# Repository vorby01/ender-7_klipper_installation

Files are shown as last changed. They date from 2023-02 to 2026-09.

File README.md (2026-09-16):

# Ender-7 Klipper Install
Details for Installing Klipper on Creality Ender 7 with BLTouch (Use at own risk)(Work in Progress)
- The ender-7 was my first 3d printer and these files show my learning curve into FDM printing with the ender-7

- Notes:
  - Ender-7 inbuilt screen will no longer work, incompatable with Klipper (creality wont release source code)
  - Installing Klipper if settings are incorrect the printer can crash/break
  
- - - -
- ### Printer Details
  - #### Creality Ender-7 Core-XY 3D Printer
    - (Early model with leadshine DM542 microstep drivers for X and Y)(purchased 2021/08/08)
  - ##### Modifications (2023/01/21) (as of)
    - Creality BL Touch Auto Bed Leveling Kit for Ender-7 (No Longer Available)(https://www.creality3d.online/collections/auto-bed-leveling-kit)
    - Embrace Making, Creality Ender 7 PEI Magnetic Flex Build Plate (https://embracemaking.com/products/copy-of-pei-magnetic-flex-build-plate-systems)
    - Tiny Machines 3D, Ender 7 Bed Stability Upgrade + Z-Axis Linear Rail Upgrade (https://www.tinymachines3d.com/products/ender-7-z-axis-upgrade-with-linear-rails-and-dual-lead-screws)
    - TH3D, Aluminum Bed Spacers (https://www.th3dstudio.com/product/aluminum-bed-spacers-pack-of-4/)

  - ##### Modifications (2023/02/18)
    - ADXL345 (Klipper Resonance Compensation)

  - ##### Modifications (2023/07/16)
    - Mosquito Magnum Hotend (New 50w Heater, Thermister(300))
    - Lgx Lite Extruder (Direct Drive)
    - Custom designed mounts for hotend and extruder on printables.com

- - - -           
- ### Klipper Host Machine
  - Raspberry Pi4
    - Running: Mainsail OS

- - - -
20260917 updated to markdown syntax
## File Descriptions:
- 00_Prerequisite info.md - Some information the should be collected before starting, eg, default firmware settings(Marlin: M503), microcontroller/board(Creality CR-FDM-v2.4.S1_v101), pin hardware names

- 01_Install mainsailOS.md - Process to install MainsailOS on raspberry pi

- 02_Klipper config and install.md - Process to build klipper printer.cfg and flash microcontroller/board

- 03_Testing and calibration.md - Process for testing klipper is functional and ready to print

- 04_Klipper macros.md - Some Klipper macros and using with PrusaSlicer

- 05_Extruder maximum flow.md - Processes for determing printers maximum flow rate/speed

- 06_Pressure advance.md - Configure and use klipper pressure advance

- 07_Resonance compensation.md - Install and use ADXL345 accelerometer to minimise printer resonance (input shaping) (max_accel: x_max=18400, y_max=11500)
 
## Pictures
### Ender 7 2023/01/21
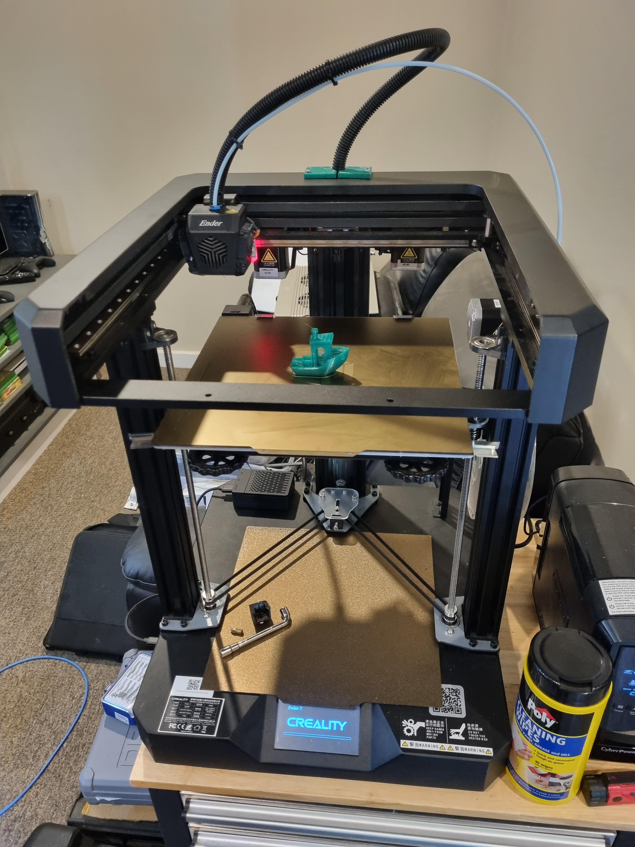
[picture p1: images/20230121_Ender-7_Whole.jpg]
Ender-7


### Ender 7 2023/07/16
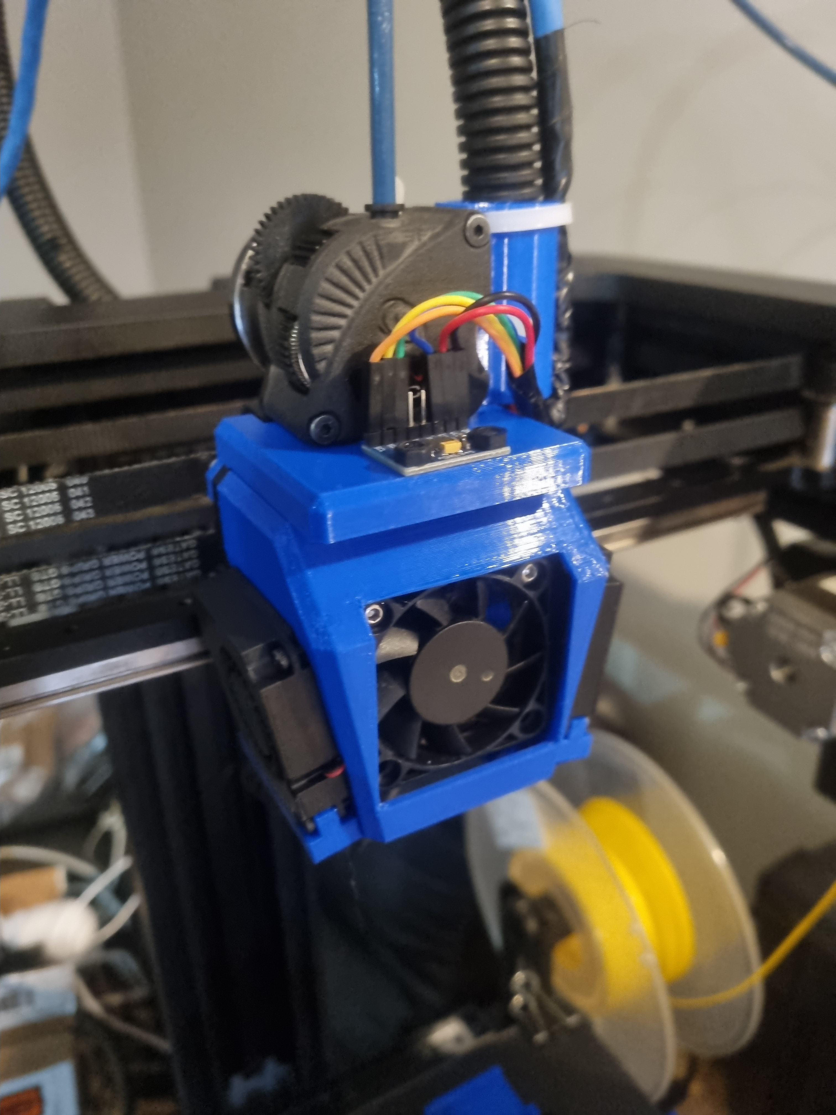
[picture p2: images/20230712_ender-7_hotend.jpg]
Ender-7_mosquito_magnum


### Ender-7 2023/08/17 hotend_upgrade_v2
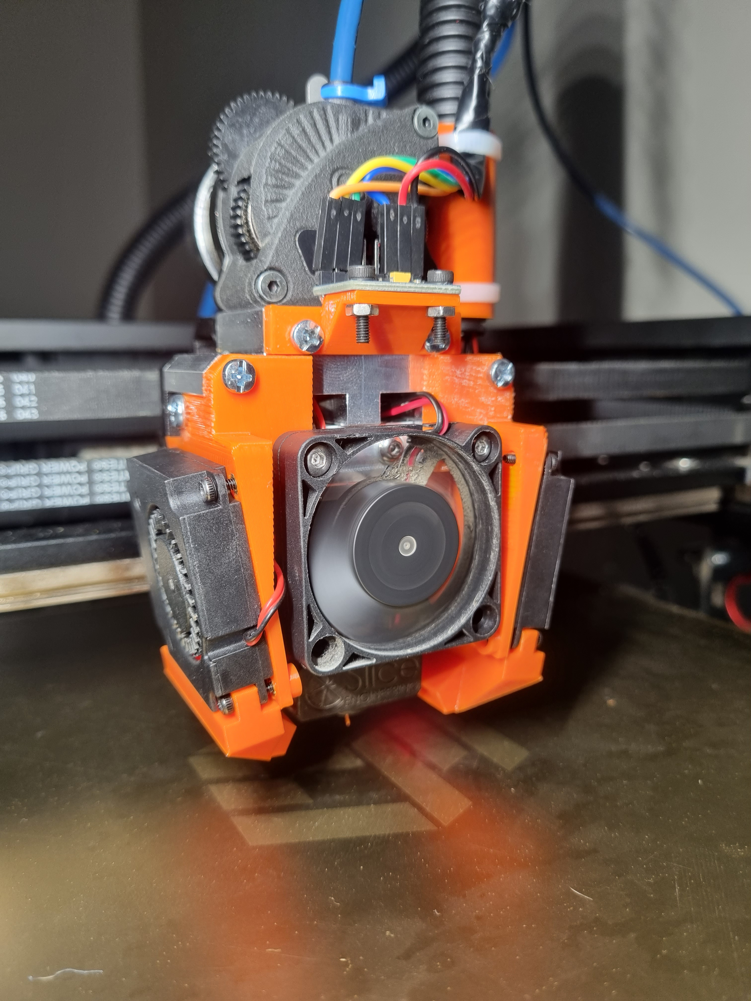
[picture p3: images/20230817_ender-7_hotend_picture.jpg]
Ender-7_mosquitto_magnum_v2


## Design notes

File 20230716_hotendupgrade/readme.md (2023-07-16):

Creality Ender-7 Hotend Upgrade to Mosquito Magnum and Lgx Lite extruder as direct drive

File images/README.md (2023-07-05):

###### Max Extrusion Test 80mm/s to 250mm/s
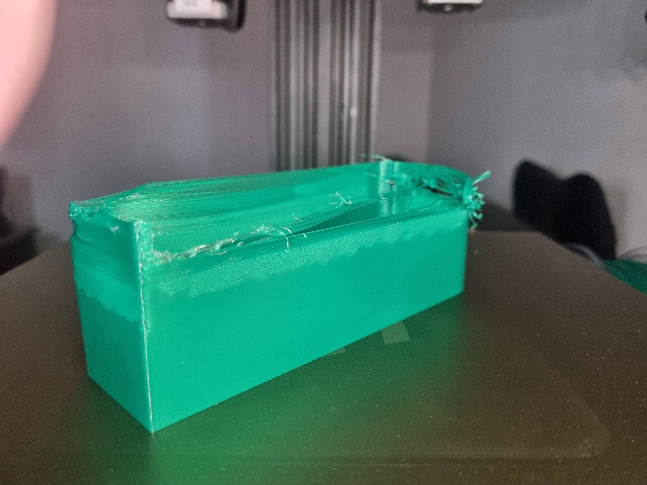
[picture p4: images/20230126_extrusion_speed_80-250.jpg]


##### Ender-7 ADXL345 Mount
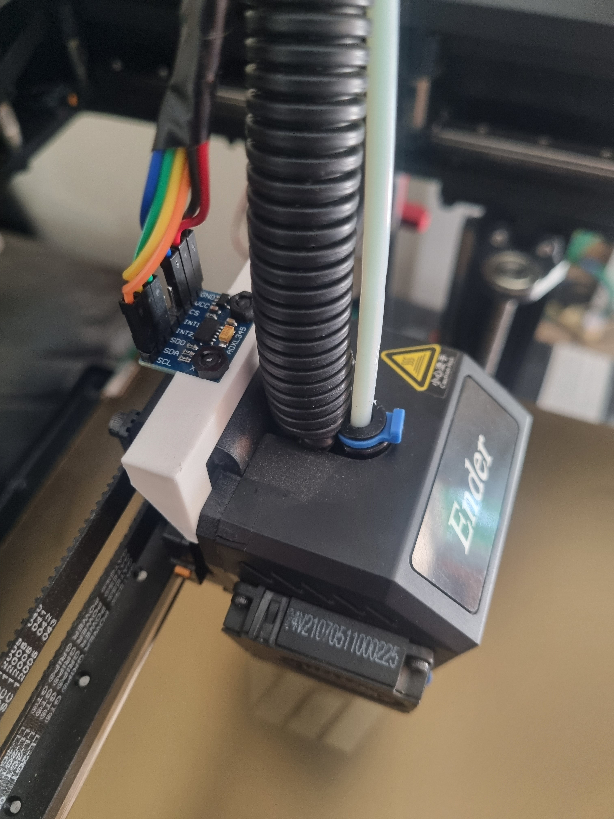
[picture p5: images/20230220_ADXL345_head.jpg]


###### Kilpper First Benchy 21/01/23 (2h 22m) (PrusaSlicer Base Ender 7 settings) 
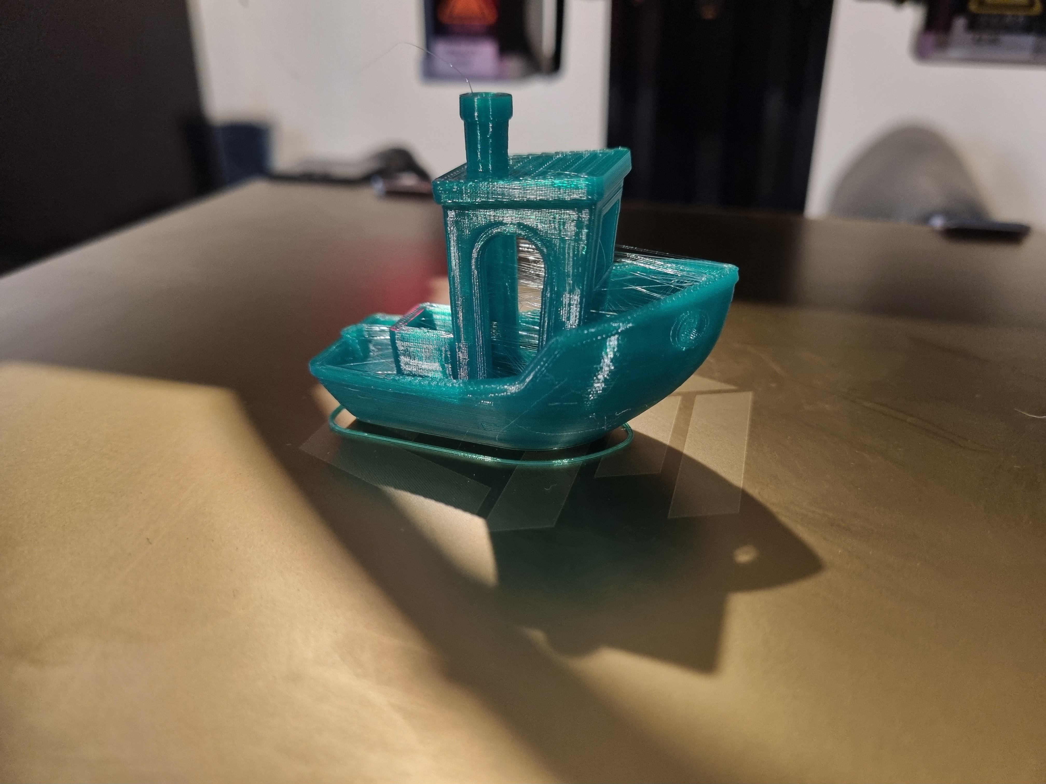
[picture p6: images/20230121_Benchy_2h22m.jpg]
benchy1


###### Benchy 23/01/23 (1h 32m)
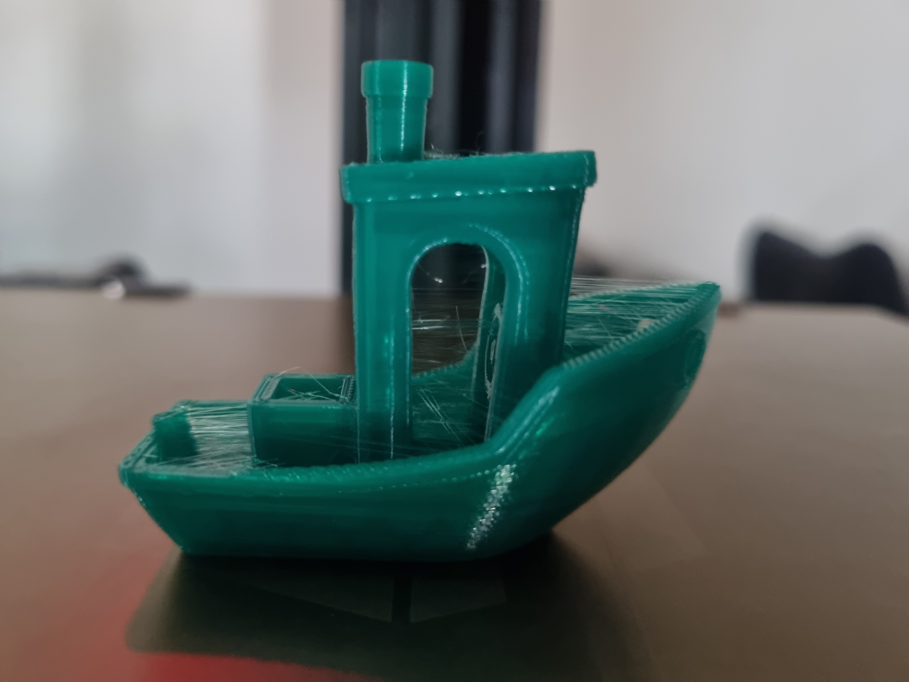
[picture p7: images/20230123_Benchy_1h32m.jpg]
benchy2


###### Benchy 24/01/23 (1h 20m)
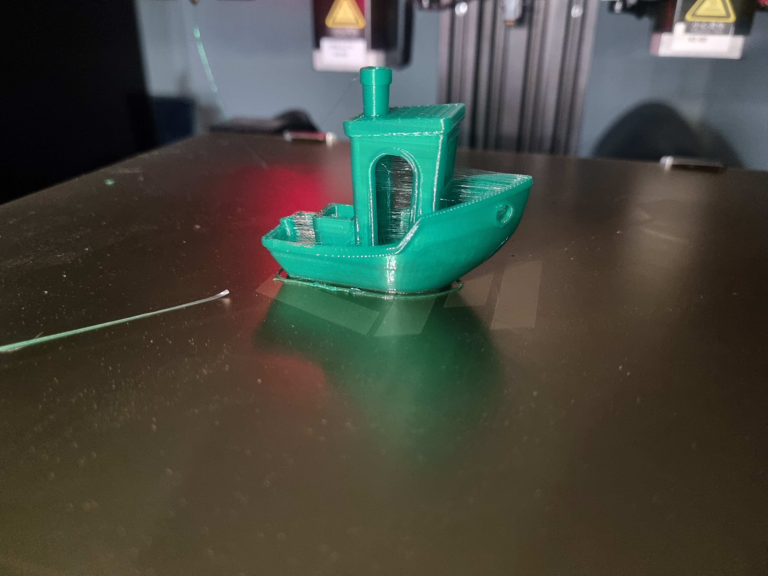
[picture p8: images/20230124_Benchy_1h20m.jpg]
benchy3


###### Benchy 05/07/23 (40m)
20230705 3DBenchy 40min (Top/Bottom Layers,3)(Perminiters,2)(Infill,10%)
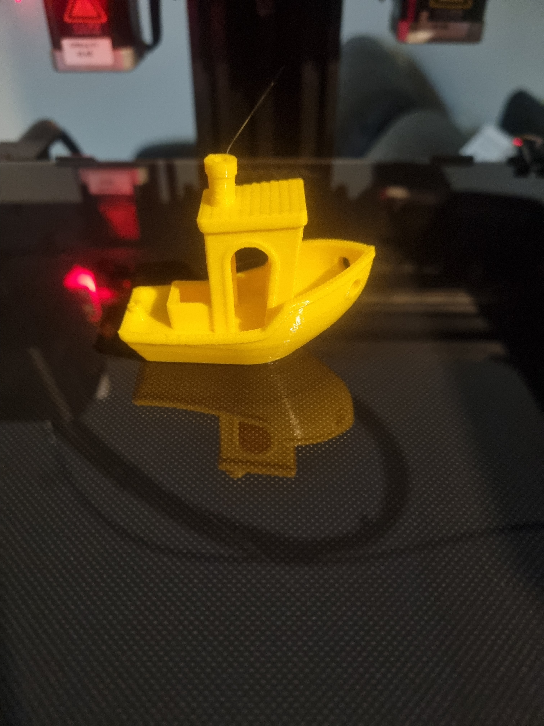
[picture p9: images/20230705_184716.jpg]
Ender-7


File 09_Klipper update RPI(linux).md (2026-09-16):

## 09_Klipper update RPI(linux)

#### Update Klipper on rpi(raspberry pi) to match updated mcu version
  - 20250125

  - SSH to RPi  
    `ssh pi@<ip_address>`

  - Navigate to Klipper directory  
    `cd ~/klipper/`

  - Klipper configure firmware
    `make menuconfig`

  - change micro-controller architecture to linux process
  - remove !PA15 (possibly still showing from mcu firmware update)

**make menuconfig (CUI)**
```
[*] Enable extra low-level configuration options
    Micro-controller Architecture (Linux proces) --->
() GPIO pins to set at micro-controller startup
```

  - Compile Klipper firmware for rpi
    - Stop Klipper service  
      `sudo service klipper stop`

    - Compile firmware  
      `make flash`

    - Start Klipper service  
      `sudo service klipper start`

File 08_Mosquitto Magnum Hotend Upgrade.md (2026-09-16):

## 08_Mosquitto Magnum Hotend Upgrade

- #### Hotend Blower Fans (EFC-04D24L) 
  - Yellow = positive, Blue = negative
  - replaced stock fans due to fault on one.

- #### Lgx Lite Extruder
  - Connector: JST-XH 4-pin connector
  - Motor gear : 10 teeth
  - Motor length: 20 mm
  - Motor Diameter: 36mm
  - Step Angle : 1.8 degree (200 steps per rotation)
  - Max Torque at : 1800 PPS
  - Max operating Temperature / Current : 120℃ / 750 mA
  - Manufacturer : LDO
  - Manufacturer SKU : LDO-36STH20-1004AHG(XH)
  - retraction speed : 35 mm/s
  - retraction distance (bowden) : ~5 mm (0.4 + tube length[mm] x 0.015)
  - retraction distance (direct drive) for rigid materials : 0.4 mm
  - retraction distance (direct drive) for soft materials : 3 mm

- #### Change of stepper motor will require adjustment of Vref for extruder (Default reading Vref 1.19v)
  - Formula for TMC stepper drivers is Vref = `( I * 2.5 ) / Imax`
    - I is the target current value measured in Amps 
    - Imax is 1.77 on regular mode and 1.2 on SilentStepSticks mode
  - Bondtech recommended vref of between .45 - .65

- min vref (0.45 * 2.5) / 1.77 = 0.64
- max vref (0.65 * 2.5) / 1.77 = 0.92
> vref between 0.67v - 0.92v

(0.55 * 2.5) / 1.77 = 0.78v

- #### Update Klipper Config to suit Lgx Lite Extruder
  - e-steps value : 562 using 16 microsteps; 1124 using 32 microsteps. 
  - rotation_distance = `full_steps_per_rotation * microsteps / steps_per_mm`
  - rotation_distance = 200 * 16 / 562
  > rotation_distance = 5.7

  - Change extruder direction to suit Lgx-Lite Extruder

**printer.cfg**
```
[extruder] #Driver, Creality Board (TMC2208) (Lgx-Lite Extruder)
dir_pin: PB3  #!PB3 = default direction, PB3 = reverse extruder dimension
```

- #### Update Klipper Config to suit new thermister
  - Slice engineering thermister(300)(ATC Semitec 104NT-4-R025H42G)

**printer.cfg**
```
[extruder] #Driver, Creality Board (TMC2208) (Lgx-Lite Extruder)
sensor_type: ATC Semitec 104NT-4-R025H42G
```

  - Calibrate new thermister  
    `PID_CALIBRATE HEATER=extruder TARGET=215`

  - Calibrate new nozzle offset  
    `PROBE_CALIBRATE`

- #### 2023_07_19 Input shaping (Resonance Compensation)
  - Check connection to accelerometer in mainsailos  
    `ACCELEROMETER_QUERY`
    
  - Measure axes noise (range ~1-100) (1000+ quality issues)  
    `MEASURE_AXES_NOISE`

  - Measure resonance (per axis)(generates CSV files)  
    `TEST_RESONANCES AXIS=X`  
    `TEST_RESONANCES AXIS=Y`

  - Process generated CSV files (Requires SSH login)  
    `~/klipper/scripts/calibrate_shaper.py /tmp/resonances_x_*.csv -o /tmp/shaper_calibrate_x.png`
    > output:  
    Fitted shaper 'mzv' frequency = 63.2 Hz (vibrations = 0.0%, smoothing ~= 0.051)  
    To avoid too much smoothing with 'mzv', suggested max_accel <= 11800 mm/sec^2

    `~/klipper/scripts/calibrate_shaper.py /tmp/resonances_y_*.csv -o /tmp/shaper_calibrate_y.png`
    > output:  
    Fitted shaper 'mzv' frequency = 45.2 Hz (vibrations = 1.3%, smoothing ~= 0.100)  
    To avoid too much smoothing with 'mzv', suggested max_accel <= 6000 mm/sec^2

  - Update klipper printer.cfg

**printer.cfg**
```
[input_shaper]
shaper_type_x: mzv
shaper_freq_x: 63.2
shaper_type_y: mzv
shaper_freq_y: 45.2

[printer]
max_accel: 10000           #x_max=11800, y_max=6000
```

  - To recalibrate after adjustment (Input Shaper auto-calibration (re-calibration)(does not update max_accel))  
    `SHAPER_CALIBRATE`  
    `SAVE_CONFIG`

- #### 2023_08_15 Pressure Advance Tuning
  - 0.4mm nozzle brass

  - Slicer 
    - Set zero infill, and a coarse layer height (the layer height should be around 75% of the nozzle diameter). Make sure any "dynamic acceleration control" is disabled in the slicer.
    - Layer Height: 0.75 * 0.4 = 0.3
    - Layer Width: 1.1 * 0.4 = 0.44
    - Estimated volume: 0.44mm * 0.3mm * 100mm/s = 13.2mm^3/sec

  - Klipper  
    `SET_VELOCITY_LIMIT SQUARE_CORNER_VELOCITY=1 ACCEL=500`  
    `TUNING_TOWER COMMAND=SET_PRESSURE_ADVANCE PARAMETER=ADVANCE START=0 FACTOR=.005`

  - Start tuning tower print

  - Measure print
  - Calculate pressure advance value
    - pressure_advance = `<start> + <measured_height> * <factor>`
    0 + 30 * 0.005 = 0.15
    > pressure_advance = 0.15

  - Update klipper printer.cfg

**printer.cfg**
```
[extruder]
pressure_advance = 0.15
```

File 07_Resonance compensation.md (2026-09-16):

## 07_Resonance compensation

### Resonance compensation (requires ADXL345)
- Mount ADXL345 to print head securely
  - print mounting bracket: 20230216_ADXL345_Mount.3mf (printed on prusa_mini+)

- ##### ADXL345 to RaspberryPi4 wiring

| CAT5 cable colours |  |
|---|---|
| Green  | Green-White  |
| Orange | Orange-White |
| Blue | Blue-White |
| Brown  | Brown-White  |

- Recommended twisted pairing (minimum interferance) (SPI wiring)
  - GND+MISO
  - 3.3V+MOSI
  - SCLK+CS

- Raspberry Pi Wiring

| RPi pinout |  | | | | |
|-----|---|---|---|---|---|
| Pin | GPIO | ADXL345 | SPI  | Colour | CAT5 |
| 17  | 3.3v | VCC | VCC  | RED | Orange |
| 19  | GPIO 10 | SDA | MOSI | YELLOW | Orange-White |
| 20  | GND | GND | | BLACK  | Green-White  |
| 21  | GPIO 9  | SDO | MISO | GREEN  | Green |
| 23  | GPIO 11 | SCL | SCLK | ORANGE | Blue-White |
| 24  | GPIO 8  | CS | CS | BLUE | Blue |

- RPi4 to ADXL345 wiring (CAT5 pairs)

| ADXL345 pinout | | |
|---|---|---|
| ADXL345 | Colour | CAT5 Colour  |
| | | |
| GND | BLACK  | Green-White  |
| SDO | GREEN  | Green |
| | | |
| 3.3 | RED | Orange |
| SDA | YELLOW | Orange-White |
| | | |
| SCL | ORANGE | Blue-White |
| CS | BLUE | Blue |

- ##### Additional required software installation
  - RPi SSH (Terminal)  
    `ssh pi@<ip_address>`

  `sudo apt update`  
  `sudo apt install python3-numpy python3-matplotlib libatlas-base-dev`  
  `~/klippy-env/bin/pip install -v numpy`

- ##### Ensure SPI is enabled  
  `sudo raspi-config`
  > interfacing options > enable SPI

- ##### Enable rpi host as secondary MCU in klipper (read ADXL345)
  - install start script (run klipper_mcu before klippy process)  
    `cd ~/klipper/`  
    `sudo cp ./scripts/klipper-mcu.service /etc/systemd/system/`  
    `sudo systemctl enable klipper-mcu.service`

  - Build and flash code for raspberry pi (dir: ~/klipper/)
    - Create configuration menu (open gui)  
      `make menuconfig`

    - Choose a processor model
      > select Linux process

      > quit and save

    - Stop Klipper service  
      `sudo service klipper stop`

    - Flash Raspberry Pi as secondary mcu  
      `make flash`
      - Installing micro-controller code to /usr/local/bin/

    - Start Klipper service  
      `sudo service klipper start`

    - Confim klipper_mcu service running  
      `sudo systemctl status klipper_mcu.service`

- ##### View raspberry pi gpio pins function/status
  - Install gpiochip
    `sudo apt-get install gpiod`

  - Detect gpiochip
    `gpiodetect`

  - Detect pins
    `gpioinfo`

- ##### Add to printer.cfg (ADXL345)

**printer.cfg**
```
[mcu rpi]
serial: /tmp/klipper_host_mcu

[adxl345]
cs_pin: rpi:None

[resonance_tester]
accel_chip: adxl345
probe_points:
125, 125, 20  # an example
```

- ##### Measuring the resonances
  - Check Connection in mainsailOS  
    `ACCELEROMETER_QUERY`
    > output: accelerometer values (x, y, z): 296.082377, -1110.308913, 9346.365076

  - MEASURE_AXES_NOISE (range ~1-100) (1000+ quality issues)  
    `MEASURE_AXES_NOISE`

  - Measure adxl345 (M112 to abort) (manual resonance compensation)
    `TEST_RESONANCES AXIS=X`
    > output: Resonances data written to /tmp/resonances_x_20230217_173259.csv file

    `TEST_RESONANCES AXIS=Y`
    > output: Resonances data written to /tmp/resonances_y_20230217_173616.csv file

- ##### Process generated CSV files (SSH)

  `~/klipper/scripts/calibrate_shaper.py /tmp/resonances_x_*.csv -o /tmp/shaper_calibrate_x.png`
  > output:  
  ```
  Fitted shaper 'zv' frequency = 85.0 Hz (vibrations = 6.2%, smoothing ~= 0.028)  
  To avoid too much smoothing with 'zv', suggested max_accel <= 28200 mm/sec^2  
  Fitted shaper 'mzv' frequency = 79.0 Hz (vibrations = 0.5%, smoothing ~= 0.035)  
  To avoid too much smoothing with 'mzv', suggested max_accel <= 18400 mm/sec^2  
  Fitted shaper 'ei' frequency = 98.4 Hz (vibrations = 0.5%, smoothing ~= 0.035)  
  To avoid too much smoothing with 'ei', suggested max_accel <= 18000 mm/sec^2  
  Fitted shaper '2hump_ei' frequency = 109.8 Hz (vibrations = 0.0%, smoothing ~= 0.047)  
  To avoid too much smoothing with '2hump_ei', suggested max_accel <= 13400 mm/sec^2  
  Fitted shaper '3hump_ei' frequency = 137.2 Hz (vibrations = 0.0%, smoothing ~= 0.046)  
  To avoid too much smoothing with '3hump_ei', suggested max_accel <= 13800 mm/sec^2  
  Recommended shaper is mzv @ 79.0 Hz
  ```

  `~/klipper/scripts/calibrate_shaper.py /tmp/resonances_y_*.csv -o /tmp/shaper_calibrate_y.png`
  > output: 
  ```
  Fitted shaper 'zv' frequency = 66.6 Hz (vibrations = 10.8%, smoothing ~= 0.041)
  To avoid too much smoothing with 'zv', suggested max_accel <= 17300 mm/sec^2
  Fitted shaper 'mzv' frequency = 62.4 Hz (vibrations = 0.0%, smoothing ~= 0.052)
  To avoid too much smoothing with 'mzv', suggested max_accel <= 11500 mm/sec^2
  Fitted shaper 'ei' frequency = 75.6 Hz (vibrations = 0.3%, smoothing ~= 0.056)
  To avoid too much smoothing with 'ei', suggested max_accel <= 10600 mm/sec^2
  Fitted shaper '2hump_ei' frequency = 94.0 Hz (vibrations = 0.0%, smoothing ~= 0.062)
  To avoid too much smoothing with '2hump_ei', suggested max_accel <= 9800 mm/sec^2
  Fitted shaper '3hump_ei' frequency = 113.0 Hz (vibrations = 0.0%, smoothing ~= 0.065)
  To avoid too much smoothing with '3hump_ei', suggested max_accel <= 9300 mm/sec^2
  Recommended shaper is mzv @ 62.4 Hz
  ```

  - Processed CSV output graphs:  
    `/tmp/shaper_calibrate_x.png`  
    `/tmp/shaper_calibrate_y.png`

  - Add to printer.cfg (manual calibration settings)
**printer.cfg**
```
[input_shaper]
shaper_type_x: mzv
shaper_freq_x: 79.0
shaper_type_y: mzv
shaper_freq_y: 62.4

[printer]
max_accel: 10000           #x_max=18400, y_max=11500
```

- ##### Input Shaper auto-calibration (re-calibration)(does not update max_accel) (mainsailOS)
  `SHAPER_CALIBRATE`  
  `SAVE_CONFIG`

- ##### Resonance Compensation Test Print
  - Download model [Klipper ringing tower](https://www.klipper3d.org/prints/ringing_tower.stl)

  - PrusaSlicer settings:
    > - layer height 0.2
    > - infill and top layers set to 0
    > - use 1-2 perimeters
    > - external perimeters 80-100mm
    > - minimum layer time max 3 seconds
    > - slicer dynamic acceleration control disabled

  - MainsailOS web interface (Klipper)
    - Set square_corner_velocity: 5

    - Increase max_accel_to_decel  
      `SET_VELOCITY_LIMIT ACCEL_TO_DECEL=7000`

    - Disable pressure advance  
      `SET_PRESSURE_ADVANCE ADVANCE=0`

    - If [input_shaper] exists in printer.cfg  
      `SET_INPUT_SHAPER SHAPER_FREQ_X=0 SHAPER_FREQ_Y=0`

    - Set shaper type (deafult: MZV)  
      `SET_INPUT_SHAPER SHAPER_TYPE=MZV`

    - Execute printing variable command  
      `TUNING_TOWER COMMAND=SET_VELOCITY_LIMIT PARAMETER=ACCEL START=1500 STEP_DELTA=500 STEP_HEIGHT=5`

    - **Start print of ringing_tower**

    - Measure oscillations
      - Count number of oscillations inside measurement
        - N = oscillations
          D = distance (mm)
          V = velocity (mm/sec)

    - Calculate ringing frequency  
      `V * N / D = Hz`

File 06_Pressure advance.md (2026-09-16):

## 06_Pressure advance

### Pressure Advance (advanced extrusion calibration)
- Requires e-steps/flow-rate calibration first
- Specific to each filament

- ##### Download Klipper pressure advance square tower
  - [https://www.klipper3d.org/prints/square_tower.stl](https://www.klipper3d.org/prints/square_tower.stl)

- ##### Slicer settings (square_tower.stl) 
> - Zero infill
> - Coarse layer height (75% of nozzle diameter)(0.4 nozzle = 0.3 layer height)
> - Any kind of slicer dynamic acceleration is disabled
> - Use a high speed (eg,100mm/s) (prusaslicer default:40mm/s)(extruder max flow rate may need to measured first)

- ##### Prepare for test (klipper commands before starting print)
  `SET_VELOCITY_LIMIT SQUARE_CORNER_VELOCITY=1 ACCEL=500`

  - For direct drive extruder  
    `TUNING_TOWER COMMAND=SET_PRESSURE_ADVANCE PARAMETER=ADVANCE START=0 FACTOR=.005`
  - For long bowden extruders  
    `TUNING_TOWER COMMAND=SET_PRESSURE_ADVANCE PARAMETER=ADVANCE START=0 FACTOR=.020`

- ##### Print square_tower.stl
  - If corners are no longer printing well print can be cancelled

  - Measure with calipers from bottom of print to where corners look best
    - eg, height= 30mm

- ##### Calculate pressure advance (bowden)
  - pressure_advance = `<start> + <measured_height> * <factor>`
  - 0 + (30 * 0.02) = 0.6

  > Typical pressure advance values are between 0.050 and 1.000

- ##### Update printer.cfg with pressure advance value

**printer.cfg**
```
[extruder]
pressure_advance = 0.6
```

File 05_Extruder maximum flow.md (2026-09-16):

## 05_Extruder maximum flow

### Determine extruder maximum flow rate(mm^3/s)(maximum printing speed)

##### **Method 1** (Estimate from extruder feed rate)(no consideration for quality)
- Maximum Feed rate/Melting rate (extruder)(issue commands from mainsailOS web interface)
  - Set e to relative  
    `M83`
  - Set and wait for nozzle temp (210C)(PLA)  
    `M109 S210`

- Increase the extrusion speed until the extruder starts to lose steps then take last value  
  Start at 1mm/s extrude 50mm (F60 = 60mm/min = 1mm/s)  

  | Command       | Feed rate |              |
  |---------------|-----------|--------------|
  | `G1 E50 F60`  | #1mm/s    |              |
  | `G1 E50 F120` | #2mm/s    |              |
  | `G1 E50 F180` | #3mm/s    |              |
  | `G1 E50 F240` | #4mm/s    |              |
  | `G1 E50 F300` | #5mm/s    |              |
  | `G1 E50 F360` | #6mm/s    |              |
  | `G1 E50 F420` | #7mm/s    |              |
  | `G1 E50 F480` | #8mm/s    |              |
  | `G1 E50 F540` | #9mm/s    |              |
  | `G1 E50 F600` | #10mm/s   | losing steps |

- Convert mm/min to mm/sec
  - 540 / 60 = 9
  > Max feed rate = 9mm/sec

- Determine filament cross section
  - Diameter: 1.75mm
  - Radius = 1.75 / 2 = 0.875mm
  - Cross section = pi * 0.875^2 = 2.405mm^2

- #### Approximate maximum flow rate (theoretical limit)
  - maximum_flow_rate(mm^3/sec) = `<max_extrusion_speed(mm/sec)> * <filament_cross_section(mm^2)>`
  - 9 * 2.405 = 21.645mm^3/sec
  > Max flow rate = 21.645mm^3/sec

- #### Approximate max speed (theoretical limit)
  - Recommnded line width: `1.2 * nozzle`
  - 1.2 * 0.4 = 0.48mm
  - speed(mm/sec) = `<volumetric_flow(mm^3/sec)> / <layer_height(mm)> / <line_width(mm)>`
  - 21.645 / 0.2 / 0.48 = 225.469mm/sec
  > Max speed = 225.469mm/sec

- #### Approximate max volumetric flow (theoretical limit)
  - volumetric_flow(mm^3/sec) = `<speed(mm/sec)> * <layer_height(mm)> * <line_width(mm)>`
  - 225.469 * 0.2 * 0.48 = 21.645mm^3
  > Max volume = 21.645mm^3

##### **Method 2** Print and measure for maximum flow (based on actual printed quality)
- print model 20230124_external_speed_test_2_0.2mm_PLA_MINI_23m.gcode

- gcode details:
  > - nozzle: 0.4
  > - line_width: 0.48
  > - layer_height: 0.2
  > - perimeters: 1
  > - material: PLA
  > - Temp_bed: 60
  > - Temp_nozzle: 215

| Height (mm)  | Perimeter speed |
|---|---|
| 0-0.5 | 60mm/s  |
| 0.5-5 | 80mm/s  |
| 5-10 | 100mm/s |
| 10-15 | 120mm/s |
| 15-20 | 140mm/s |
| 20-25 | 160mm/s |
| 25-30 | 180mm/s |
| 30-35 | 200mm/s |
| 35-40 | 220mm/s |
| 40-45 | 240mm/s |
| 45-50 | 250mm/s |

- Measure from base up to where under extrusion begins
  - 25mm = 160mm/s

- Calculate maximum volumetric flow rate from measurement
  - 160 * 0.2 * 0.48 = 15.36mm^3/sec

- Confirm Calculation (speed)
  - 15.36 / 0.2 / 0.48 = 160mm/sec

- #### Max filament feed rate
  - 15.36 / 2.405 = 6.387mm/sec
  > Max feed rate = 6.387mm/sec

- #### Approximate maximum flow rate
  - maximum_flow_rate(mm^3/sec) = `<max_extrusion_speed(mm/sec)> * <filament_cross_section(mm^2)>`
  - 6.387mm/sec * 2.405mm^2 = 21.645mm^3/sec
  > Max flow rate = 15.361mm^3/sec

#### For more accurate flow rate calculation CNC Kitchen
- [https://www.cnckitchen.com/blog/extrusion-system-benchmark-tool-for-fast-prints](https://www.cnckitchen.com/blog/extrusion-system-benchmark-tool-for-fast-prints)
  - will require a milligram scale
- [https://www.printables.com/model/160335-hotened-benchmark-test-g-codes](https://www.printables.com/model/160335-hotened-benchmark-test-g-codes)

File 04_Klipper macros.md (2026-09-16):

## 04_Klipper macros

### Klipper Macros
- Create macros.cfg
  > macros can be nested in printer.cfg but simpler to seperate file for ease of use

**macros.cfg**
```
[gcode_macro PRINT_START]
gcode:
  {% set BED_TEMP = params.BED_TEMP|default(60)|float %}                # Extract bed temp from gcode as variable
  {% set EXTRUDER_TEMP = params.EXTRUDER_TEMP|default(220)|float %}     # Extract extruder temp from gcode as variable
  G90                           # Use absolute coordinates
  SET_GCODE_OFFSET Z=0.0        # Reset the g-code z offset
  M83                           # Extruder relative mode
  M107                          # Set fan off
  G28                           # Home printer axis
  M104 S150                     # preheat extruder, minimise oozing
  M190 S{BED_TEMP}              # Set and wait for bed heating
  BED_MESH_CALIBRATE            # Automatic bed leveling
  G1 Z50 F240                   # Move z_axis down to 50mm
  M109 S{EXTRUDER_TEMP}         # Set and wait for hotend heating
  #Prime Nozzle (On build plate left)
  G1 X2 Y10 F3000               # Move x,y axis
  G1 Z0.28 F240                 # Move z axis
  G92 E0                        # reset extruder distance to 0
  G1 X2.0 Y140 E10 F1500        # first pass prime
  G1 X2.3 Y140 F5000            # offset
  G92 E0                        # reset extruder distance to 0
  G1 X2.3 Y10 E10 F1200         # second pass prime
  G92 E0                        # reset extruder distance to 0

[gcode_macro PRINT_STOP]
gcode:
  G91                           # Use relative coordinates
  G1 Z10                        # Lower z axis by 10mm
  G28 X Y                       # Move gantry out of way to home
  M140 S0                       # turn off heatbed
  M104 S0                       # turn off temperature
  M107                          # turn off fan
  #M84 X Y E                    # disable motors (will require re-homing axis)
  #M84                          # disable all motors (will require re-homing axis)

[gcode_macro CANCEL_PRINT]
description: Cancel running print
rename_existing: CANCEL_PRINT_BASE
gcode:
  TURN_OFF_HEATERS
  CANCEL_PRINT_BASE
  G91                           # Use relative coordinates
  G1 Z10                        # Lower z axis by 10mm
  G90                           # Use absolute coordinates
  G28 X Y                       # Move gantry out of way to home
  #M84                          # Disable all motors (will require re-homing axis)
```

- Upload macros.cfg to Klipper
  > Mainsail_os > settings > machine > config files > upload file > macros.cfg

- Update printer.cfg to include macros.cfg
  - append: [include macros.cfg]
  - save and restart (apply changes)

### Update PrusaSlicer for use with Klipper

- PrusaSlicer Start g-code

**start gcode**
```
;E7 Klipper start macro
M104 S0
M140 S0
PRINT_START EXTRUDER_TEMP={first_layer_temperature[0]} BED_TEMP={first_layer_bed_temperature[0]}
```

- PrusaSlicer End g-code

**end gcode**
```
;E7 Klipper stop macro
PRINT_STOP
```

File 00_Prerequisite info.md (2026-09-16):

### Ender-7 Hardware Information
- Board: Creality CR-FDM-v2.4.S1_v101
  - Power input: 24v
  - Processor: ARM® Cortex®-M3 STM32F1 Microcontroller IC 32-Bit Single-Core 72MHz 512KB (512K x 8) FLASH
    - STM32F103RET6
    - 32bit
    
### Ender-7 Firmware Information (Marlin 1 - Command Output) (Prior to Klipper install)
Command for output from printer serial connection:  
`M503                                                             # Report Settings`

```
Recv:   G21    ; Units in mm (mm)
Recv: 
Recv:   M200 S0 D1.75                                          #M200 - Set Filament Diameter
Recv:   M92 X200.00 Y200.00 Z400.00 E140.00                    #M92  - Set Axis Steps-per-unit
Recv:   M203 X500.00 Y500.00 Z10.00 E60.00                     #M203 - Set Max Feedrate
Recv:   M201 X500.00 Y500.00 Z100.00 E5000.00                  #M201 - Print Move Limits
Recv:   M204 P500.00 R1000.00 T500.00                          #M204 - Set Starting Acceleration
Recv:   M205 B20000.00 S0.00 T0.00 X8.00 Y8.00 Z0.40 E5.00     #M205 - Set Advanced Settings [B -Minimum segment time (µs)][S -Minimum feedrate for print moves (units/s)][T -Minimum feedrate for travel moves (units/s)][X -X max jerk (units/s)][Y -Y max jerk (units/s)][Z -Z max jerk (units/s)][E -E max jerk (units/s)]
Recv:   M206 X0.00 Y0.00 Z0.00                                 #M206 - Set Home Offsets
Recv:   M420 S1 Z10.00                                         #M420 - Bed Leveling State [S -Set enabled or disabled][Z -Set Z fade height (Requires ENABLE_LEVELING_FADE_HEIGHT)]
Recv:   M301 P12.50 I0.70 D60.00                               #M301 - Set Hotend PID [P -Proportional value][I -Integral value][D -Derivative value]
Recv:   M304 P327.11 I19.20 D1393.45                           #M304 - Set Bed PID
Recv:   M413 S0                                                #M413 - Power-loss Recovery
Recv:   M851 X30.00 Y27.00 Z-2.60                              #M851 - XYZ Probe Offset
```

### CR-FDM-v2.4.S1_v101 Pinout (hardware names)
> [! preceding name to indicate reverse polarity]  
> [^ preceding hardware pull-up resistor]  
> [~ preceding hardware pull-down resistor]  

```
[stepper_x]
step_pin: PC2
dir_pin: PB9
enable_pin: !PC3
endstop_pin: ^PA5

[stepper_y]
step_pin: PB8
dir_pin: !PB7
enable_pin: !PC3
endstop_pin: ^PA6

[stepper_z]
step_pin: PB6
dir_pin: PB5
enable_pin: !PC3
endstop_pin: ^PA7

[extruder]
step_pin: PB4
dir_pin: !PB3
enable_pin: !PC3
heater_pin: PA1
sensor_pin: PC5

[heater_bed]
heater_pin: PA15
sensor_pin: PC4

[fan]
pin: PA0

[filament_switch_sensor filament_sensor]
switch_pin: !PA4

[bltouch]
sensor_pin: ^PB1
control_pin: PB0
```

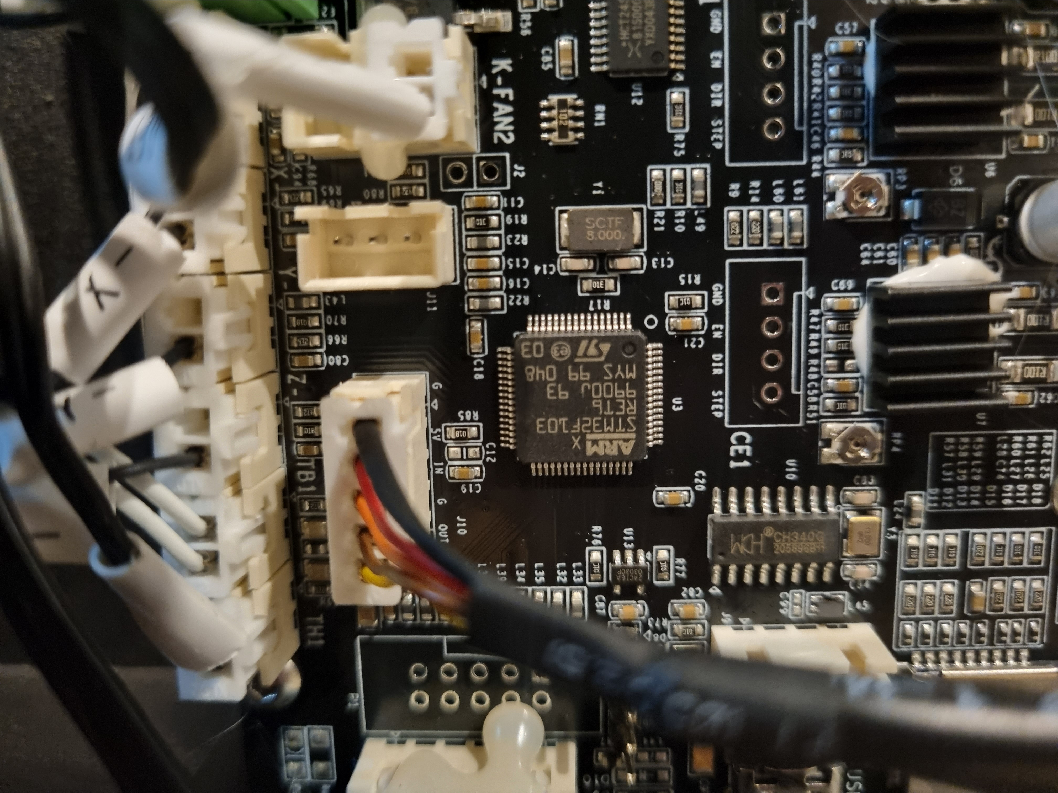
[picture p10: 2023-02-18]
images/20230116_ender-7_board_close_1.jpg

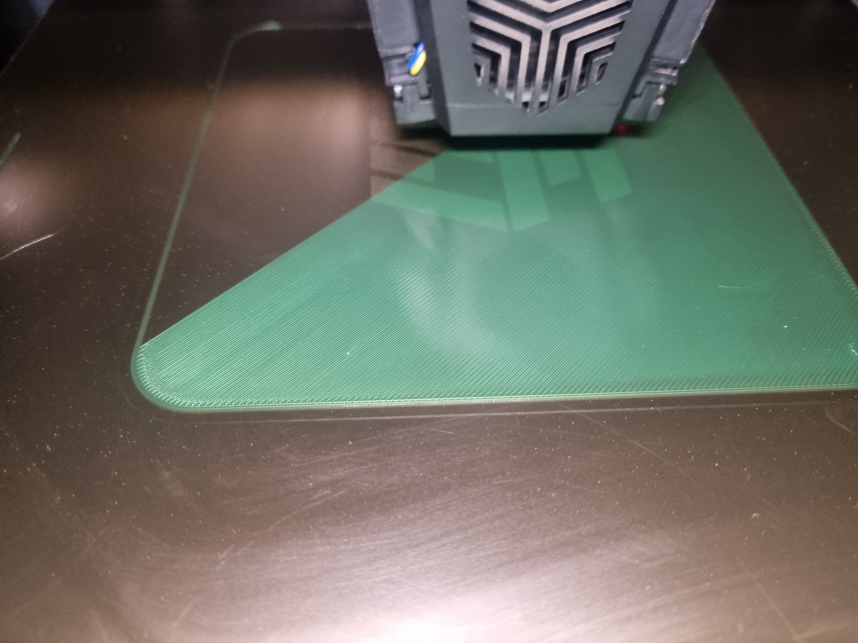
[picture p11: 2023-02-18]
images/20230125_first_layer_100mm.jpg

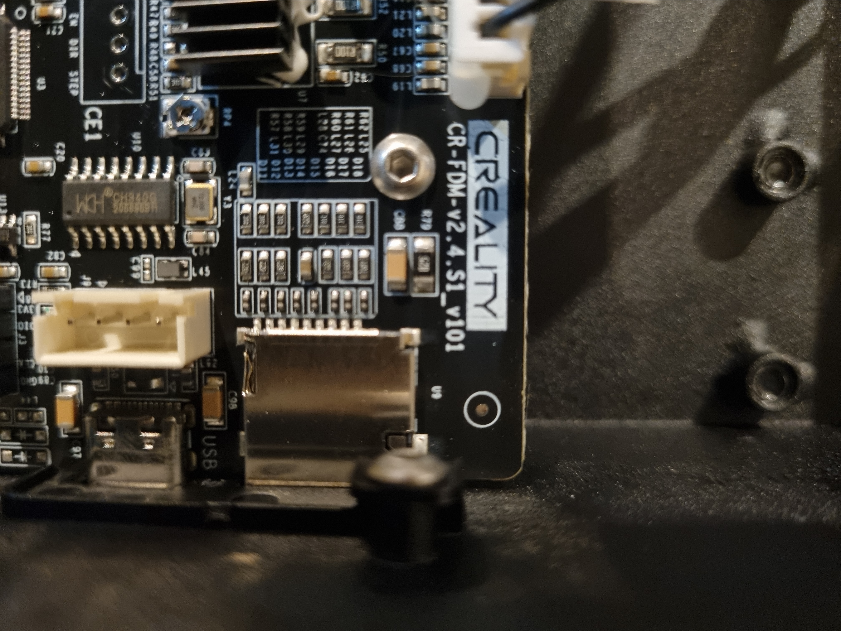
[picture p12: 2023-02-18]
images/20230116_ender-7_board_close_2.jpg

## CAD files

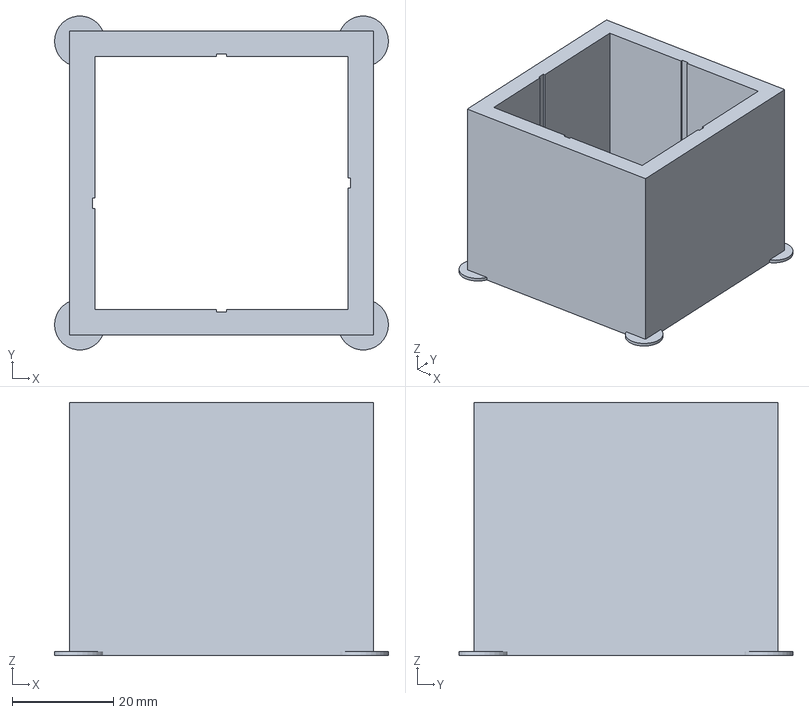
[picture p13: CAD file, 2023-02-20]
models/square_tower.3mf
66.0 x 65.9 x 50.0 mm

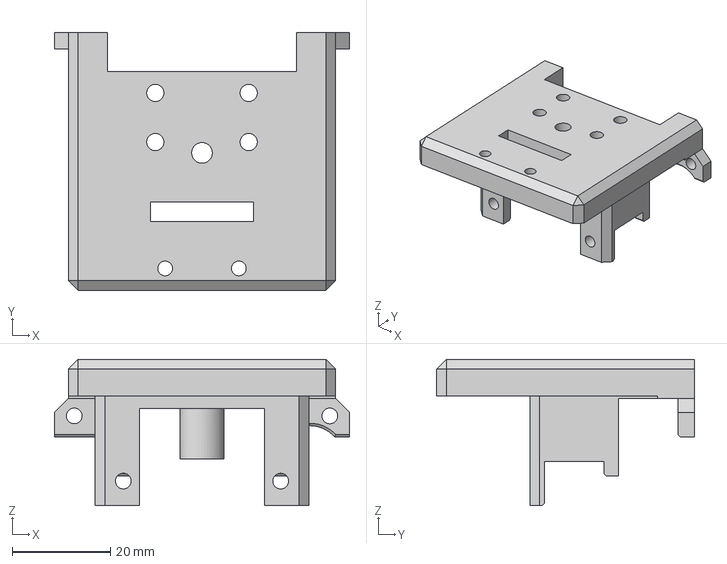
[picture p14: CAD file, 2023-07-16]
20230716_hotendupgrade/20230713_ender-7_lgx_lite_extruder_mount.step
60.0 x 52.5 x 29.8 mm

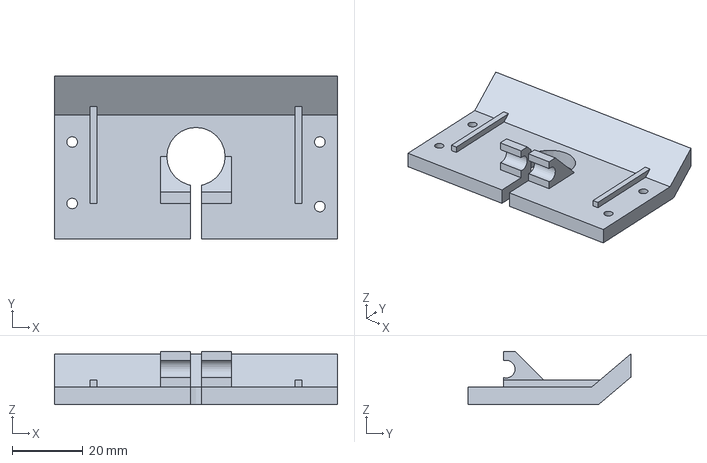
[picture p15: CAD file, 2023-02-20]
models/20230118_ender-7_wire_support.3mf
80.0 x 46.0 x 15.0 mm

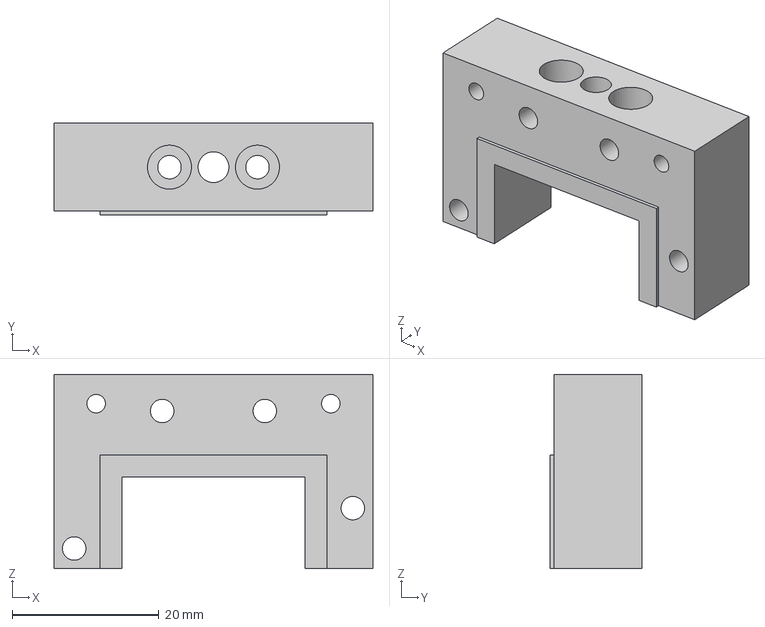
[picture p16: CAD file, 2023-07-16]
20230716_hotendupgrade/20230713_ender-7_mosquito_hotend_mount.step
43.5 x 12.5 x 26.5 mm

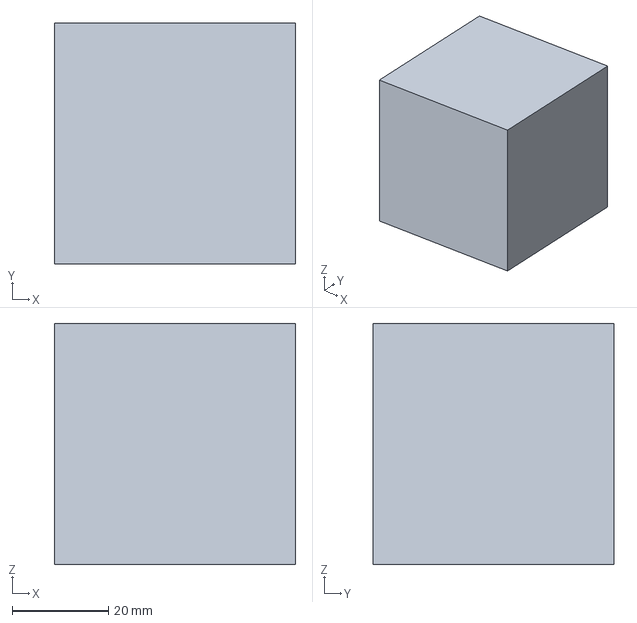
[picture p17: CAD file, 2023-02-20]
models/20200120_50mm_cube_flow_calibration.3mf
50.0 x 50.0 x 50.0 mm

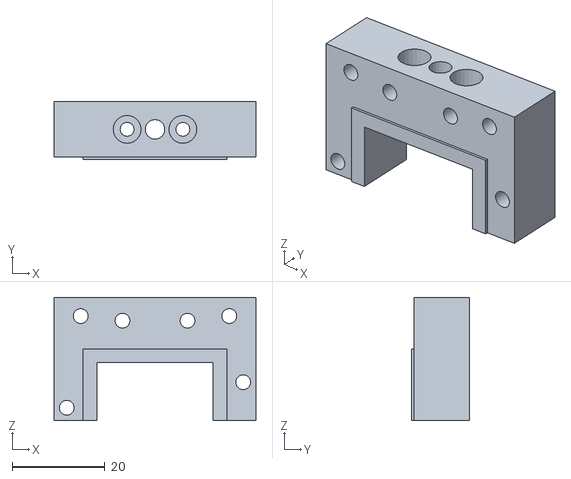
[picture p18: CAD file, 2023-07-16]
20230716_hotendupgrade/20230710_ender-7_mosquito_magnum_adapter_v1.stl
43.5 x 12.5 x 26.5

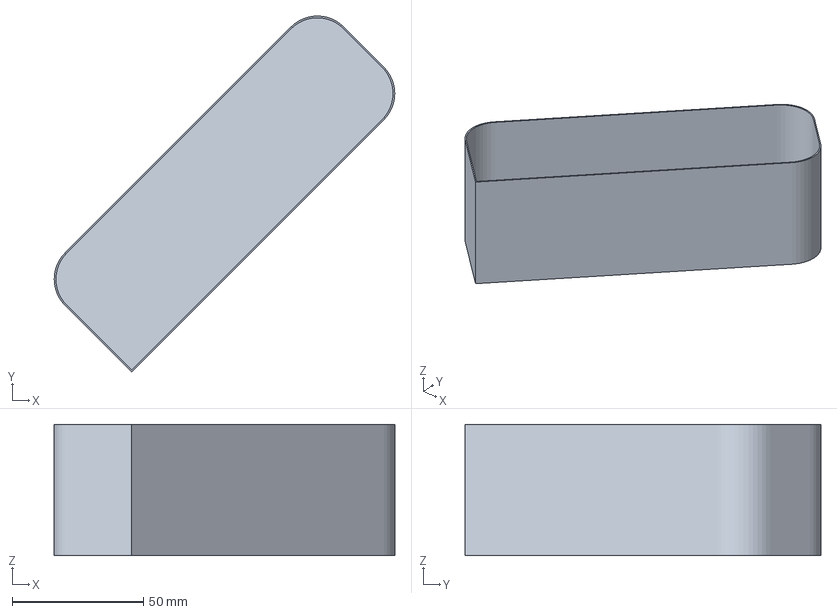
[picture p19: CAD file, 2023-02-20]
models/20230124_external_speed_test_80-250.3mf
129.7 x 135.6 x 50.0 mm

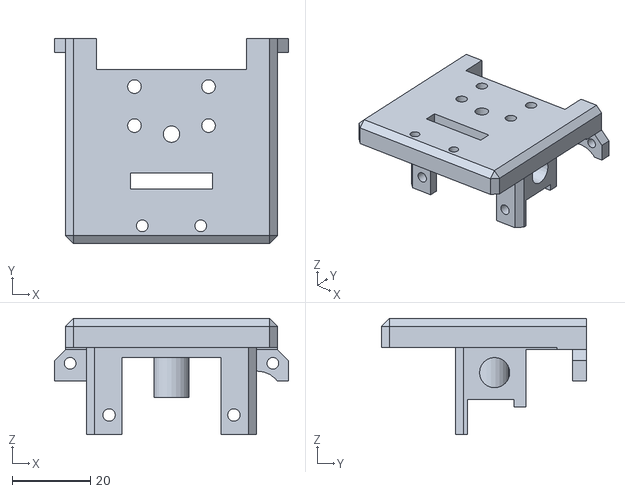
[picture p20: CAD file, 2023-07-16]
20230716_hotendupgrade/20230710_ender-7_lgx_light_extruder_mount_adxl345.stl
60.0 x 52.5 x 29.8

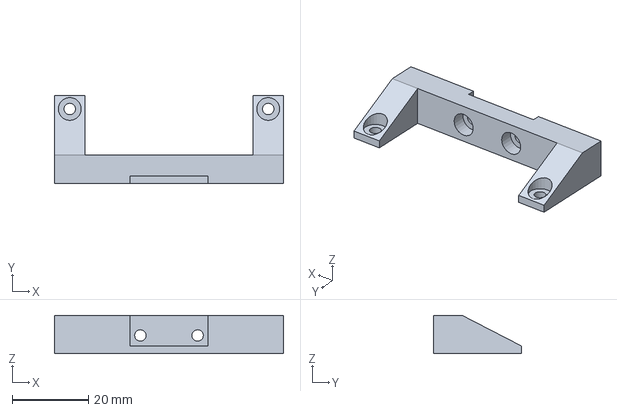
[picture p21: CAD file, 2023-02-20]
models/20230216_ADXL345_Mount.3mf
60.0 x 23.0 x 10.0 mm

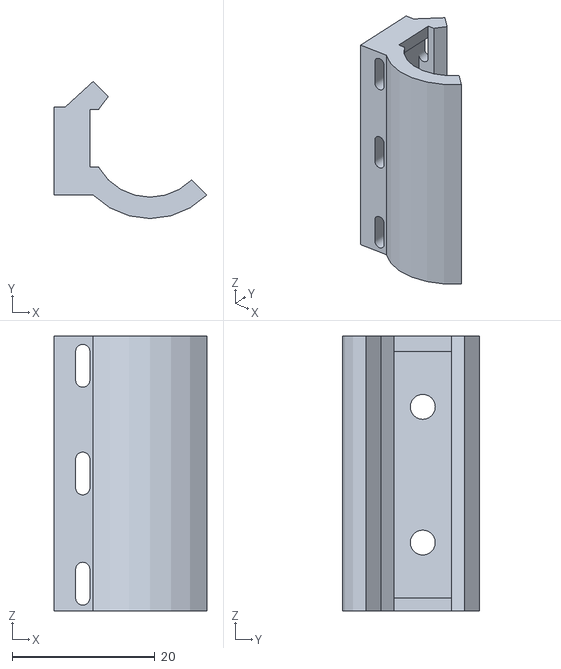
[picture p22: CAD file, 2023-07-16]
20230716_hotendupgrade/20230710_ender-7_cable_sleeve_support.stl
21.4 x 19.2 x 38.5

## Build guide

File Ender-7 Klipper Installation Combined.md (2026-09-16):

# Ender-7 Klipper Installation

----------------------------------------------------------------------------------------------------

20260917 updated to markdown syntax
## File Descriptions:
- 00_Prerequisite info.md - Some information the should be collected before starting, eg, default firmware settings(Marlin: M503), microcontroller/board(Creality CR-FDM-v2.4.S1_v101), pin hardware names

- 01_Install mainsailOS.md - Process to install MainsailOS on raspberry pi

- 02_Klipper config and install.md - Process to build klipper printer.cfg and flash microcontroller/board

- 03_Testing and calibration.md - Process for testing klipper is functional and ready to print

- 04_Klipper macros.md - Some Klipper macros and using with PrusaSlicer

- 05_Extruder maximum flow.md - Processes for determing printers maximum flow rate/speed

- 06_Pressure advance.md - Configure and use klipper pressure advance

- 07_Resonance compensation.md - Install and use ADXL345 accelerometer to minimise printer resonance (input shaping) (max_accel: x_max=18400, y_max=11500)

----------------------------------------------------------------------------------------------------

## 00_Prerequisite info

### Ender-7 Hardware Information
- Board: Creality CR-FDM-v2.4.S1_v101
  - Power input: 24v
  - Processor: ARM® Cortex®-M3 STM32F1 Microcontroller IC 32-Bit Single-Core 72MHz 512KB (512K x 8) FLASH
    - STM32F103RET6
    - 32bit
    
### Ender-7 Firmware Information (Marlin 1 - Command Output) (Prior to Klipper install)
Command for output from printer serial connection:  
`M503                                                             # Report Settings`

```
Recv:   G21    ; Units in mm (mm)
Recv: 
Recv:   M200 S0 D1.75                                          #M200 - Set Filament Diameter
Recv:   M92 X200.00 Y200.00 Z400.00 E140.00                    #M92  - Set Axis Steps-per-unit
Recv:   M203 X500.00 Y500.00 Z10.00 E60.00                     #M203 - Set Max Feedrate
Recv:   M201 X500.00 Y500.00 Z100.00 E5000.00                  #M201 - Print Move Limits
Recv:   M204 P500.00 R1000.00 T500.00                          #M204 - Set Starting Acceleration
Recv:   M205 B20000.00 S0.00 T0.00 X8.00 Y8.00 Z0.40 E5.00     #M205 - Set Advanced Settings [B -Minimum segment time (µs)][S -Minimum feedrate for print moves (units/s)][T -Minimum feedrate for travel moves (units/s)][X -X max jerk (units/s)][Y -Y max jerk (units/s)][Z -Z max jerk (units/s)][E -E max jerk (units/s)]
Recv:   M206 X0.00 Y0.00 Z0.00                                 #M206 - Set Home Offsets
Recv:   M420 S1 Z10.00                                         #M420 - Bed Leveling State [S -Set enabled or disabled][Z -Set Z fade height (Requires ENABLE_LEVELING_FADE_HEIGHT)]
Recv:   M301 P12.50 I0.70 D60.00                               #M301 - Set Hotend PID [P -Proportional value][I -Integral value][D -Derivative value]
Recv:   M304 P327.11 I19.20 D1393.45                           #M304 - Set Bed PID
Recv:   M413 S0                                                #M413 - Power-loss Recovery
Recv:   M851 X30.00 Y27.00 Z-2.60                              #M851 - XYZ Probe Offset
```

### CR-FDM-v2.4.S1_v101 Pinout (hardware names)
> [! preceding name to indicate reverse polarity]  
> [^ preceding hardware pull-up resistor]  
> [~ preceding hardware pull-down resistor]  

```
[stepper_x]
step_pin: PC2
dir_pin: PB9
enable_pin: !PC3
endstop_pin: ^PA5

[stepper_y]
step_pin: PB8
dir_pin: !PB7
enable_pin: !PC3
endstop_pin: ^PA6

[stepper_z]
step_pin: PB6
dir_pin: PB5
enable_pin: !PC3
endstop_pin: ^PA7

[extruder]
step_pin: PB4
dir_pin: !PB3
enable_pin: !PC3
heater_pin: PA1
sensor_pin: PC5

[heater_bed]
heater_pin: PA15
sensor_pin: PC4

[fan]
pin: PA0

[filament_switch_sensor filament_sensor]
switch_pin: !PA4

[bltouch]
sensor_pin: ^PB1
control_pin: PB0
```

----------------------------------------------------------------------------------------------------

## 01_Install mainsailOS

### Install mainsailOS

#### Raspberry Pi Imager (Flash microSD card)
> Choose OS > Other specific-purpose OS > 3D printing > Mainsail OS

```
- hostname: mainsail
- enable ssh
- user: pi
- pwd: <password>
- configure/set wireless network settings
```

#### On mainsailOS First Boot
- Wait for file system to expand
- Log in to web interface
  - Update components from web interface
    > settings > machine > Update Manager

----------------------------------------------------------------------------------------------------

## 02_Klipper configuration and install

> Connect usb cable connected from RPi to printer for serial connection (serial console)

1. ### Connect with SSH to RPi4 running MainsailOS
   `ssh pi@<ip_address>`

2. ### Confirm printer serial COM port name (2023)
   `ls /dev/serial/by-id/*`

   > output: /dev/serial/by-id/usb-1a86_USB_Serial-if00-port0

   > COM port name may change after software update, may require microcontroller to be reflashed
   > - `sudo dmesg -w | grep tty` Shows kernal buffer, will display device connect/disconnect messages (device unplug/plug)
   > - Identify usb serial port (ttyUSB0)

3. ### Connect to Mainsail web interface and create klipper configuration
   Create printer.cfg for Klipper (/home/pi/printer_data/config/printer.cfg)
   > Machine > Create File > printer.cfg

**printer.cfg** (minimum config with bltouch)
```
[include mainsail.cfg]

[mcu]
serial: /dev/serial/by-id/usb-1a86_USB_Serial-if00-port0
restart_method: command
#baud: 250000

[printer]
kinematics: corexy
max_velocity: 500          # max feedrate (E7:500)(Other:300)
max_accel: 3000
max_z_velocity: 10
max_z_accel: 100

[stepper_x]
step_pin: PC2
dir_pin: PB9
enable_pin: !PC3
rotation_distance: 32
microsteps: 32
endstop_pin: ^PA5
position_endstop: 0
position_max: 250
homing_speed: 50

[stepper_y]
step_pin: PB8
dir_pin: !PB7
enable_pin: !PC3
rotation_distance: 32
microsteps: 32
endstop_pin: ^PA6
position_endstop: 250
position_max: 250
homing_speed: 50

[stepper_z]
step_pin: PB6
dir_pin: PB5
enable_pin: !PC3
rotation_distance: 8
microsteps: 16
#endstop_pin: ^PA7                            # disable to use BLTouch
#position_endstop: 3.0                        # disable to use BLTouch
endstop_pin: probe:z_virtual_endstop          # enable to use BLTouch
position_min: -3.5                            # enable to use BLTouch
position_max: 300

[extruder]
step_pin: PB4
dir_pin: !PB3
enable_pin: !PC3
microsteps: 16
rotation_distance: 23.564                    # Re-tune to suit
full_steps_per_rotation: 200
nozzle_diameter: 0.400
filament_diameter: 1.750
max_extrude_only_distance: 200.0
pressure_advance = 0                         # 0 to disable
#HOT END VARIABLES
heater_pin: PA1
sensor_type: EPCOS 100K B57560G104F
sensor_pin: PC5
#control: pid                                #(PID_CALIBRATE HEATER=extruder TARGET=200)
pid_kp = 74.327                              # updated after PID_CALIBRATE
pid_ki = 0.985                               # updated after PID_CALIBRATE
pid_kd = 1401.994                            # updated after PID_CALIBRATE
min_temp: 0
max_temp: 230

[heater_bed]
heater_pin: PA15
sensor_type: EPCOS 100K B57560G104F
sensor_pin: PC4
#control: pid                                #(PID_CALIBRATE HEATER=heater_bed TARGET=60)
pid_kp = 19.588                              # updated after PID_CALIBRATE
pid_ki = 1.005                               # updated after PID_CALIBRATE
pid_kd = 95.493                              # updated after PID_CALIBRATE
min_temp: 0
max_temp: 75

[fan]
pin: PA0          # Hotend additional fans

[filament_switch_sensor filament_sensor]
pause_on_runout: true
switch_pin: !PA4

[bltouch]                 # enable for BLTouch (requires self_test after each firmware restart)
sensor_pin: ^PB1
control_pin: PB0
z_offset: 2.550          # initial safe value, get correct value by PROBE_CALIBRATE
x_offset: -28.28
y_offset: -28.28

[safe_z_home]                       # BLTouch home x,y axis then move to centre and home z
home_xy_position: 125, 125          # Change coordinates to the center of your print bed
speed: 50
z_hop: 10                           # Move up 10mm
z_hop_speed: 5

[bed_mesh]
speed: 120
horizontal_move_z: 10       #lift z between movements
mesh_min: -25, -25          # x, y (x: 0-28.28=-28.28, -28.28+250= 221.72)
mesh_max: 190, 190
probe_count: 4
```

4. ### Create Klipper.bin and flash to microcontroller (printer)

   > ### 20230508 update, lost connection to mainboard
   > - USB serial port changed after software update
   > - `sudo dmesg -w | grep tty` Shows kernal buffer, will display device connect/disconnect messages (device unplug/plug)
   > - Locate new usb serial (ttyUSB0)
   > - update printer.cfg serial: ***/dev/ttyUSB0***

   #### Navigate to Klipper directory
   `cd ~/klipper/`

   #### Klipper configure microcontroller firmware
   `make menuconfig`
   > !PA15 required to prevent bed heater turning on automatically at printer start

   ```
   [*] Enable extra low-level configuration options
       Micro-controller Architecture (STMicroelectronics STM32) --->
       Processor model (STM32F103) --->
   [ ] Disable SWD at startup (for GigaDevice stm32f103 clones)
       Bootloader offset (28Kib bootloader) --->
       Clock Reference (8 MHz crystal) --->
       Communication interface (Serial (on USART1 PA10/PA9)) --->
   (250000) Baud rate for serial port
   (!PA15) GPIO pins to set at micro-controller startup
   ```

   #### Compile Klipper firmware for microcontroller
   Stop Klipper service:  
   `sudo service klipper stop`

   Compile firmware: (output current directory)  
   `make`
   > File output: ~/klipper/out/klipper.bin

   Start Klipper service:  
   `sudo service klipper start`

   > #### Recommended to retrive printer settings with M503 before flashing to aid in configuration after flashing Klipper
   >    Example:  
   >   `M503, M92 X200.00 Y200.00 Z400.00 E140.00, Axis Steps-per-unit (e-steps)`

5. ### Flash firmware to microcontroller
   a. Download compiled firmware (klipper.bin) from RPi to local machine for transfer to microSD card
      > WinSCP - GUI SSH File transfer client for windows
      >> download: ~/klipper/out/klipper.bin

   b. Rename klipper.bin to unique filename (must not match any previous filename)(add date)

   c. Upload klipper.bin to micro-sd card

   d. With printer off ensure usb cable is disconnected (nothing connected during flashing)

   e. Insert micro-sd card and turn printer on

   f. Wait for board to flash (wait several min) (screen will no longer display current status)

   g. Connect usb and login to mainsailOS web interface to confirm flashing is complete

### DO NOT PRINT yet still need to test and calibrate

----------------------------------------------------------------------------------------------------

## 03_Testing and calibration

### Thoroughly test printer (warning can crash printer, be ready to turn of power if somthing goes wrong)

#### Checklist  
- [ ] Individually check heated bed and hotend temps (set small values and check if temp readings are as expected)
- [ ] Check functionality of all endstops
- [ ] Check homing
- [ ] Check extruder operation(direction)
- [ ] Perform PID tuning for heated bed and hotend
- [ ] Check your extruder is able to extrude the instructed amount of filament 
  - [ ] Calibrate e-steps
  - [ ] Calibrate flow rate

### Login to MainsailOS web interface and issue commands

1. #### Test bed heater

   #### Set heater_bed temp check heat then turn off and check for cool down (safe operation)
   `SET_HEATER_TEMPERATURE HEATER=heater_bed TARGET=30`

   `SET_HEATER_TEMPERATURE HEATER=heater_bed TARGET=0`

   ### Set heater_bed temp check heat then turn off and check for cool down (safe operation)
   `SET_HEATER_TEMPERATURE HEATER=extruder TARGET=50`

   `SET_HEATER_TEMPERATURE HEATER=extruder TARGET=0`

2. #### Check endstops operation (with BLTouch)
   - Disable motors  
     `M83`
     - Manually move print head away from end stops to center
     - Manually lower print bed out of way

   - Check endstops status  
     `QUERY_ENDSTOPS`
     > output: x:open y:open z:open

   - Manually press and hold each endstop switch (X,Y) and check operation
     `QUERY_ENDSTOPS`
     > output: x:triggered y:triggered z:open

   - Test BLTouch operation (Z axis)  
     `bltouch_debug command=pin_down`
     > pin goes down, light goes off

     `bltouch_debug command=pin_up`
     > pin goes up, red light goes on

   - Test BLTouch Z endstop operation  
     `bltouch_debug command=pin_down`  
     `bltouch_debug command=touch_mode`  
     `query_probe`
     > return: probe: open

   - Slightly press and hold bltouch probe so it lights up but does not fully retract and query  
     `query_probe`
     > return: probe: triggered

     `QUERY_ENDSTOPS`
     > return: x:open y:open z:triggered

   - If probe blinks (probe state error)  
     Reset probe if fault(blinking)  
     `bltouch_debug command=reset`

     `bltouch_debug command=self_test`
     > while test runs, pin goes down and up repeatedly, red light stays on

3. #### Check Homing
   - Verify stepper motor operation (Move axis 1mm back and forth 10 times)

     `STEPPER_BUZZ STEPPER=stepper_x`

     `STEPPER_BUZZ STEPPER=stepper_y`

     `STEPPER_BUZZ STEPPER=stepper_z`

   - Verify direction and homeing(endstop) per axis
     - Home X axis  
     `G28 x`
     - Home Y axis  
     `G28 y`
     - Home Z axis (Probe should drop first then bed will start moving)  
     `G28 z`
  
4. #### Calibrate Z offset
   `probe_calibrate`
   - Adjust z-offset (Peice of paper just dragging between nozzle and bed)

     `testz=-0.1`

     `testz=+0.1`

     > When happy with adjustment enter accept command in console  
     > `accept`

   - Verify accuracy of Z offset  
     `probe_accuracy`
     - 0.0125 or better, 0.025 no worse
     > output: standard deviation of 0.002077
      
5. #### Check extruder operation (direction) (no filament)
   - Set E to relative  
     `M83`

   - Extrude 100mm  
     `G1 E100 F100`

   - Retract 100mm  
     `G1 E-100 F100`

6. #### Perform PID tuning for heated bed and hotend 
   > #### Feed in filament so hotend is not empty for test

   `PID_CALIBRATE HEATER=heater_bed TARGET=60`
   > output: PID parameters: pid_Kp=74.515 pid_Ki=1.153 pid_Kd=1204.353

   `PID_CALIBRATE HEATER=extruder TARGET=200`
   > output: PID parameters: pid_Kp=21.862 pid_Ki=1.139 pid_Kd=104.939

   - When PID tuning complete save  
     `save_config`

7. #### Calibrate Extruder (Calibrate e-steps) (Klipper: rotation_distance)
   - ##### **Method_1** Obtaining rotation_distance from steps_per_mm (e-steps)(approximation)
     - Retrieve e-steps from firmware (Marlin) before flashing microcontroller with Klipper
       `M503`
       > output: M92 X200.00 Y200.00 Z400.00 E140.00
       >  - 140 e-steps

     - Calculate rotation distance
       - rotation_distance = `<full_steps_per_rotation> * <microsteps> / <steps_per_mm>`
       > - 1.8 degree motor (full rotation = 200 steps (360/1.8=200))
       > - 16 microsteps
       > - 200 * 16 / 140 = 22.857
       - rotation_distance = 22.857mm

   - ##### **Method_2** Obtaining rotation_distance from measure and trim
     - Heat extruder to 210C with filament (PLA)
     - Mark Filament at 100mm from intake to extruder
     - Mark Filament at 120mm from intake to extruder

     - Extrude 100mm filament (low speed minimul pressure in extruder)
       - Set Extruder relative  
         `G91`
       - Extrude 100mm  
         `G1 E100 F100`

     - Measure remaining distance to mark (120mm mark to beginning of extruder)
       > Remaining Measurement = 23mm

     - actual_extrude_distance = `<initial_mark_distance> - <subsequent_mark_distance>`
       > 120 - 23 = 97mm

     - Previous e-steps
       > 140 e-steps / 100mm = 1.4 step per mm

     - Current e-steps
       - Actual length extruded = `120mm – (Length from the extruder to mark after extruding)`
       > 120mm - 23mm = 97mm

     - Accurate steps/mm = `Old steps/mm × Actual length extruded`
       > 1.4steps/mm * 97mm = 135.8steps/mm

     - New rotation_distance for Klipper
       - rotation_distance = `<full_steps_per_rotation> * <microsteps> / <steps_per_mm>`
       > 200steps * (16microsteps / 135.8steps/mm) = 23.564mm

8. #### Calibrate flow rate (specific to each filament)
   - PrusaSlicer (extrusion multiplier)
     - Create/download a flow rate calibration model (50mm solid cube) and slice

     - Slicer print settings:
       - Layer Height: 0.2mm (or set to your normal printer layer height)
       > PrusaSlicer > print settings > layers and perimeters > Layer height

       - Line Width: 0.4 (wall thickness)
       > PrusaSlicer > print settings > advanced > default extrusion width

       - Wall Count(Perimeters): 1
       > PrusaSlicer > print settings > layers and perimeters > Perimeters

       - Infill Density: Set to 0%
       - Top layers: set to 0 to make cube hollow
       > PrusaSlicer > print settings > layers and perimeters > Solid layers > Top

       - Print Speed: Set to your normal wall printing speed
       > PrusaSlicer > print settings > layers and perimeters > Perimeters (default 40mm/s)

     - Slicer filament settings
       - PrusaSlicer Generic PLA
       > Nozzle, First Layer:215C, Other Layers:215C  
       > Bed,    First Layer:60C,  Other Layers:60C

   - **Print Model with settings above**

   - Measure each wall thickness at center on print with calipers
     > measurements: 0.36, 0.4, 0.39, 0.35
     - 0.36 + 0.4 + 0.39 + 0.35 = 1.5mm
     - 1.5 / 4 = 0.375mm average wall thickness

   - Calculate flow rate
     - New flow rate (%) = `(0.4 ÷ average wall width) × 100`
     - (0.4 / 0.375) * 100 = 106.667%
     - Extrusion Multiplier: 106.667% = 1.07

   - Update PrusaSlicer Extrusion Multiplier (recommended range: 0.9-1.1)
     > Filament Settings > Filament > Extrusion multiplier = 1.07

----------------------------------------------------------------------------------------------------

## 04_Klipper macros

### Klipper Macros
- Create macros.cfg
  > macros can be nested in printer.cfg but simpler to seperate file for ease of use

**macros.cfg**
```
[gcode_macro PRINT_START]
gcode:
  {% set BED_TEMP = params.BED_TEMP|default(60)|float %}                # Extract bed temp from gcode as variable
  {% set EXTRUDER_TEMP = params.EXTRUDER_TEMP|default(220)|float %}     # Extract extruder temp from gcode as variable
  G90                           # Use absolute coordinates
  SET_GCODE_OFFSET Z=0.0        # Reset the g-code z offset
  M83                           # Extruder relative mode
  M107                          # Set fan off
  G28                           # Home printer axis
  M104 S150                     # preheat extruder, minimise oozing
  M190 S{BED_TEMP}              # Set and wait for bed heating
  BED_MESH_CALIBRATE            # Automatic bed leveling
  G1 Z50 F240                   # Move z_axis down to 50mm
  M109 S{EXTRUDER_TEMP}         # Set and wait for hotend heating
  #Prime Nozzle (On build plate left)
  G1 X2 Y10 F3000               # Move x,y axis
  G1 Z0.28 F240                 # Move z axis
  G92 E0                        # reset extruder distance to 0
  G1 X2.0 Y140 E10 F1500        # first pass prime
  G1 X2.3 Y140 F5000            # offset
  G92 E0                        # reset extruder distance to 0
  G1 X2.3 Y10 E10 F1200         # second pass prime
  G92 E0                        # reset extruder distance to 0

[gcode_macro PRINT_STOP]
gcode:
  G91                           # Use relative coordinates
  G1 Z10                        # Lower z axis by 10mm
  G28 X Y                       # Move gantry out of way to home
  M140 S0                       # turn off heatbed
  M104 S0                       # turn off temperature
  M107                          # turn off fan
  #M84 X Y E                    # disable motors (will require re-homing axis)
  #M84                          # disable all motors (will require re-homing axis)

[gcode_macro CANCEL_PRINT]
description: Cancel running print
rename_existing: CANCEL_PRINT_BASE
gcode:
  TURN_OFF_HEATERS
  CANCEL_PRINT_BASE
  G91                           # Use relative coordinates
  G1 Z10                        # Lower z axis by 10mm
  G90                           # Use absolute coordinates
  G28 X Y                       # Move gantry out of way to home
  #M84                          # Disable all motors (will require re-homing axis)
```

- Upload macros.cfg to Klipper
  > Mainsail_os > settings > machine > config files > upload file > macros.cfg

- Update printer.cfg to include macros.cfg
  - append: [include macros.cfg]
  - save and restart (apply changes)

### Update PrusaSlicer for use with Klipper

- PrusaSlicer Start g-code

**start gcode**
```
;E7 Klipper start macro
M104 S0
M140 S0
PRINT_START EXTRUDER_TEMP={first_layer_temperature[0]} BED_TEMP={first_layer_bed_temperature[0]}
```

- PrusaSlicer End g-code

**end gcode**
```
;E7 Klipper stop macro
PRINT_STOP
```

----------------------------------------------------------------------------------------------------

## 05_Extruder maximum flow

### Determine extruder maximum flow rate(mm^3/s)(maximum printing speed)

##### **Method 1** (Estimate from extruder feed rate)(no consideration for quality)
- Maximum Feed rate/Melting rate (extruder)(issue commands from mainsailOS web interface)
  - Set e to relative  
    `M83`
  - Set and wait for nozzle temp (210C)(PLA)  
    `M109 S210`

- Increase the extrusion speed until the extruder starts to lose steps then take last value  
  Start at 1mm/s extrude 50mm (F60 = 60mm/min = 1mm/s)  

  | Command       | Feed rate |
  |---------------|---------  |
  | `G1 E50 F60`  | #1mm/s    |
  | `G1 E50 F120` | #2mm/s    |
  | `G1 E50 F180` | #3mm/s    |
  | `G1 E50 F240` | #4mm/s    |
  | `G1 E50 F300` | #5mm/s    |
  | `G1 E50 F360` | #6mm/s    |
  | `G1 E50 F420` | #7mm/s    |
  | `G1 E50 F480` | #8mm/s    |
  | `G1 E50 F540` | #9mm/s    |
  | `G1 E50 F600` | #10mm/s   | losing steps

- Convert mm/min to mm/sec
  - 540 / 60 = 9
  > Max feed rate = 9mm/sec

- Determine filament cross section
  - Diameter: 1.75mm
  - Radius = 1.75 / 2 = 0.875mm
  - Cross section = pi * 0.875^2 = 2.405mm^2

- #### Approximate maximum flow rate (theoretical limit)
  - maximum_flow_rate(mm^3/sec) = `<max_extrusion_speed(mm/sec)> * <filament_cross_section(mm^2)>`
  - 9 * 2.405 = 21.645mm^3/sec
  > Max flow rate = 21.645mm^3/sec

- #### Approximate max speed (theoretical limit)
  - Recommnded line width: `1.2 * nozzle`
  - 1.2 * 0.4 = 0.48mm
  - speed(mm/sec) = `<volumetric_flow(mm^3/sec)> / <layer_height(mm)> / <line_width(mm)>`
  - 21.645 / 0.2 / 0.48 = 225.469mm/sec
  > Max speed = 225.469mm/sec

- #### Approximate max volumetric flow (theoretical limit)
  - volumetric_flow(mm^3/sec) = `<speed(mm/sec)> * <layer_height(mm)> * <line_width(mm)>`
  - 225.469 * 0.2 * 0.48 = 21.645mm^3
  > Max volume = 21.645mm^3

##### **Method 2** Print and measure for maximum flow (based on actual printed quality)
- print model 20230124_external_speed_test_2_0.2mm_PLA_MINI_23m.gcode

- gcode details:
  > - nozzle: 0.4
  > - line_width: 0.48
  > - layer_height: 0.2
  > - perimeters: 1
  > - material: PLA
  > - Temp_bed: 60
  > - Temp_nozzle: 215

| Height (mm)  | Perimeter speed |
|---|---|
| 0-0.5 | 60mm/s  |
| 0.5-5 | 80mm/s  |
| 5-10 | 100mm/s |
| 10-15 | 120mm/s |
| 15-20 | 140mm/s |
| 20-25 | 160mm/s |
| 25-30 | 180mm/s |
| 30-35 | 200mm/s |
| 35-40 | 220mm/s |
| 40-45 | 240mm/s |
| 45-50 | 250mm/s |

- Measure from base up to where under extrusion begins
  - 25mm = 160mm/s

- Calculate maximum volumetric flow rate from measurement
  - 160 * 0.2 * 0.48 = 15.36mm^3/sec

- Confirm Calculation (speed)
  - 15.36 / 0.2 / 0.48 = 160mm/sec

- #### Max filament feed rate
  - 15.36 / 2.405 = 6.387mm/sec
  > Max feed rate = 6.387mm/sec

- #### Approximate maximum flow rate
  - maximum_flow_rate(mm^3/sec) = `<max_extrusion_speed(mm/sec)> * <filament_cross_section(mm^2)>`
  - 6.387mm/sec * 2.405mm^2 = 21.645mm^3/sec
  > Max flow rate = 15.361mm^3/sec

#### For more accurate flow rate calculation CNC Kitchen
- [CNC kitchen guide](https://www.cnckitchen.com/blog/extrusion-system-benchmark-tool-for-fast-prints "https://www.cnckitchen.com/blog/extrusion-system-benchmark-tool-for-fast-prints")
  - will require a milligram scale
- [Printables model](https://www.printables.com/model/160335-hotened-benchmark-test-g-codes "https://www.printables.com/model/160335-hotened-benchmark-test-g-codes")

----------------------------------------------------------------------------------------------------

## 06_Pressure advance

### Pressure Advance (advanced extrusion calibration)
- Requires e-steps/flow-rate calibration first
- Specific to each filament

- ##### Download Klipper pressure advance square tower
  - [Klipper pressure advance model](https://www.klipper3d.org/prints/square_tower.stl "https://www.klipper3d.org/prints/square_tower.stl")

- ##### Slicer settings (square_tower.stl) 
> - Zero infill
> - Coarse layer height (75% of nozzle diameter)(0.4 nozzle = 0.3 layer height)
> - Any kind of slicer dynamic acceleration is disabled
> - Use a high speed (eg,100mm/s) (prusaslicer default:40mm/s)(extruder max flow rate may need to measured first)

- ##### Prepare for test (klipper commands before starting print)
  `SET_VELOCITY_LIMIT SQUARE_CORNER_VELOCITY=1 ACCEL=500`

  - For direct drive extruder  
    `TUNING_TOWER COMMAND=SET_PRESSURE_ADVANCE PARAMETER=ADVANCE START=0 FACTOR=.005`
  - For long bowden extruders  
    `TUNING_TOWER COMMAND=SET_PRESSURE_ADVANCE PARAMETER=ADVANCE START=0 FACTOR=.020`

- ##### Print square_tower.stl
  - If corners are no longer printing well print can be cancelled

  - Measure with calipers from bottom of print to where corners look best
    - eg, height= 30mm

- ##### Calculate pressure advance (bowden)
  - pressure_advance = `<start> + <measured_height> * <factor>`
  - 0 + (30 * 0.02) = 0.6

  > Typical pressure advance values are between 0.050 and 1.000

- ##### Update printer.cfg with pressure advance value

**printer.cfg**
```
[extruder]
pressure_advance = 0.6
```

----------------------------------------------------------------------------------------------------

## 07_Resonance compensation

### Resonance compensation (requires ADXL345)
- Mount ADXL345 to print head securely
  - print mounting bracket: 20230216_ADXL345_Mount.3mf (printed on prusa_mini+)

- ##### ADXL345 to RaspberryPi4 wiring

| CAT5 cable colours
|--------|
| Green  | Green-White
| Orange | Orange-White
| Blue   | Blue-White
| Brown  | Brown-White

- Recommended twisted pairing (minimum interferance) (SPI wiring)
  - GND+MISO
  - 3.3V+MOSI
  - SCLK+CS

- Raspberry Pi Wiring

| RPi pinout |  | | | | |
|-----|---|---|---|---|---|
| Pin | GPIO | ADXL345 | SPI  | Colour | CAT5 |
| 17  | 3.3v | VCC | VCC  | RED | Orange |
| 19  | GPIO 10 | SDA | MOSI | YELLOW | Orange-White |
| 20  | GND | GND | | BLACK  | Green-White  |
| 21  | GPIO 9  | SDO | MISO | GREEN  | Green |
| 23  | GPIO 11 | SCL | SCLK | ORANGE | Blue-White |
| 24  | GPIO 8  | CS | CS | BLUE | Blue |

- RPi4 to ADXL345 wiring (CAT5 pairs)

| ADXL345 pinout | | |
|---|---|---|
| ADXL345 | Colour | CAT5 Colour  |
| | | |
| GND | BLACK  | Green-White  |
| SDO | GREEN  | Green |
| | | |
| 3.3 | RED | Orange |
| SDA | YELLOW | Orange-White |
| | | |
| SCL | ORANGE | Blue-White |
| CS | BLUE | Blue |

- ##### Additional required software installation
  - RPi SSH (Terminal)  
    `ssh pi@<ip_address>`

  `sudo apt update`  
  `sudo apt install python3-numpy python3-matplotlib libatlas-base-dev`  
  `~/klippy-env/bin/pip install -v numpy`

- ##### Ensure SPI is enabled  
  `sudo raspi-config`
  > interfacing options > enable SPI

- ##### Enable rpi host as secondary MCU in klipper (read ADXL345)
  - install start script (run klipper_mcu before klippy process)  
    `cd ~/klipper/`  
    `sudo cp ./scripts/klipper-mcu.service /etc/systemd/system/`  
    `sudo systemctl enable klipper-mcu.service`

  - Build and flash code for raspberry pi (dir: ~/klipper/)
    - Create configuration menu (open gui)  
      `make menuconfig`

    - Choose a processor model
      > select Linux process

      > quit and save

    - Stop Klipper service  
      `sudo service klipper stop`

    - Flash Raspberry Pi as secondary mcu  
      `make flash`
      - Installing micro-controller code to /usr/local/bin/

    - Start Klipper service  
      `sudo service klipper start`

    - Confim klipper_mcu service running  
      `sudo systemctl status klipper_mcu.service`

- ##### View raspberry pi gpio pins function/status
  - Install gpiochip
    `sudo apt-get install gpiod`

  - Detect gpiochip
    `gpiodetect`

  - Detect pins
    `gpioinfo`

- ##### Add to printer.cfg (ADXL345)

**printer.cfg**
```
[mcu rpi]
serial: /tmp/klipper_host_mcu

[adxl345]
cs_pin: rpi:None

[resonance_tester]
accel_chip: adxl345
probe_points:
125, 125, 20  # an example
```

- ##### Measuring the resonances
  - Check Connection in mainsailOS  
    `ACCELEROMETER_QUERY`
    > output: accelerometer values (x, y, z): 296.082377, -1110.308913, 9346.365076

  - MEASURE_AXES_NOISE (range ~1-100) (1000+ quality issues)  
    `MEASURE_AXES_NOISE`

  - Measure adxl345 (M112 to abort) (manual resonance compensation)
    `TEST_RESONANCES AXIS=X`
    > output: Resonances data written to /tmp/resonances_x_20230217_173259.csv file

    `TEST_RESONANCES AXIS=Y`
    > output: Resonances data written to /tmp/resonances_y_20230217_173616.csv file

- ##### Process generated CSV files (SSH)

  `~/klipper/scripts/calibrate_shaper.py /tmp/resonances_x_*.csv -o /tmp/shaper_calibrate_x.png`
  > output:  
  ```
  Fitted shaper 'zv' frequency = 85.0 Hz (vibrations = 6.2%, smoothing ~= 0.028)  
  To avoid too much smoothing with 'zv', suggested max_accel <= 28200 mm/sec^2  
  Fitted shaper 'mzv' frequency = 79.0 Hz (vibrations = 0.5%, smoothing ~= 0.035)  
  To avoid too much smoothing with 'mzv', suggested max_accel <= 18400 mm/sec^2  
  Fitted shaper 'ei' frequency = 98.4 Hz (vibrations = 0.5%, smoothing ~= 0.035)  
  To avoid too much smoothing with 'ei', suggested max_accel <= 18000 mm/sec^2  
  Fitted shaper '2hump_ei' frequency = 109.8 Hz (vibrations = 0.0%, smoothing ~= 0.047)  
  To avoid too much smoothing with '2hump_ei', suggested max_accel <= 13400 mm/sec^2  
  Fitted shaper '3hump_ei' frequency = 137.2 Hz (vibrations = 0.0%, smoothing ~= 0.046)  
  To avoid too much smoothing with '3hump_ei', suggested max_accel <= 13800 mm/sec^2  
  Recommended shaper is mzv @ 79.0 Hz
  ```

  `~/klipper/scripts/calibrate_shaper.py /tmp/resonances_y_*.csv -o /tmp/shaper_calibrate_y.png`
  > output: 
  ```
  Fitted shaper 'zv' frequency = 66.6 Hz (vibrations = 10.8%, smoothing ~= 0.041)
  To avoid too much smoothing with 'zv', suggested max_accel <= 17300 mm/sec^2
  Fitted shaper 'mzv' frequency = 62.4 Hz (vibrations = 0.0%, smoothing ~= 0.052)
  To avoid too much smoothing with 'mzv', suggested max_accel <= 11500 mm/sec^2
  Fitted shaper 'ei' frequency = 75.6 Hz (vibrations = 0.3%, smoothing ~= 0.056)
  To avoid too much smoothing with 'ei', suggested max_accel <= 10600 mm/sec^2
  Fitted shaper '2hump_ei' frequency = 94.0 Hz (vibrations = 0.0%, smoothing ~= 0.062)
  To avoid too much smoothing with '2hump_ei', suggested max_accel <= 9800 mm/sec^2
  Fitted shaper '3hump_ei' frequency = 113.0 Hz (vibrations = 0.0%, smoothing ~= 0.065)
  To avoid too much smoothing with '3hump_ei', suggested max_accel <= 9300 mm/sec^2
  Recommended shaper is mzv @ 62.4 Hz
  ```

  - Processed CSV output graphs:  
    `/tmp/shaper_calibrate_x.png`  
    `/tmp/shaper_calibrate_y.png`

  - Add to printer.cfg (manual calibration settings)
**printer.cfg**
```
[input_shaper]
shaper_type_x: mzv
shaper_freq_x: 79.0
shaper_type_y: mzv
shaper_freq_y: 62.4

[printer]
max_accel: 10000           #x_max=18400, y_max=11500
```

- ##### Input Shaper auto-calibration (re-calibration)(does not update max_accel) (mainsailOS)
  `SHAPER_CALIBRATE`  
  `SAVE_CONFIG`

- ##### Resonance Compensation Test Print
  - Download model [Klipper ringing tower](https://www.klipper3d.org/prints/ringing_tower.stl)

  - PrusaSlicer settings:
    > - layer height 0.2
    > - infill and top layers set to 0
    > - use 1-2 perimeters
    > - external perimeters 80-100mm
    > - minimum layer time max 3 seconds
    > - slicer dynamic acceleration control disabled

  - MainsailOS web interface (Klipper)
    - Set square_corner_velocity: 5

    - Increase max_accel_to_decel  
      `SET_VELOCITY_LIMIT ACCEL_TO_DECEL=7000`

    - Disable pressure advance  
      `SET_PRESSURE_ADVANCE ADVANCE=0`

    - If [input_shaper] exists in printer.cfg  
      `SET_INPUT_SHAPER SHAPER_FREQ_X=0 SHAPER_FREQ_Y=0`

    - Set shaper type (deafult: MZV)  
      `SET_INPUT_SHAPER SHAPER_TYPE=MZV`

    - Execute printing variable command  
      `TUNING_TOWER COMMAND=SET_VELOCITY_LIMIT PARAMETER=ACCEL START=1500 STEP_DELTA=500 STEP_HEIGHT=5`

    - **Start print of ringing_tower**

    - Measure oscillations
      - Count number of oscillations inside measurement
        - N = oscillations
          D = distance (mm)
          V = velocity (mm/sec)

    - Calculate ringing frequency  
      `V * N / D = Hz`

----------------------------------------------------------------------------------------------------

## 08_Mosquitto Magnum Hotend Upgrade

#### Hotend Blower Fans (EFC-04D24L) 
  - Yellow = positive, Blue = negative
  - replaced stock fans due to fault on one.

#### Lgx Lite Extruder
  - Connector: JST-XH 4-pin connector
  - Motor gear : 10 teeth
  - Motor length: 20 mm
  - Motor Diameter: 36mm
  - Step Angle : 1.8 degree (200 steps per rotation)
  - Max Torque at : 1800 PPS
  - Max operating Temperature / Current : 120℃ / 750 mA
  - Manufacturer : LDO
  - Manufacturer SKU : LDO-36STH20-1004AHG(XH)
  - retraction speed : 35 mm/s
  - retraction distance (bowden) : ~5 mm (0.4 + tube length[mm] x 0.015)
  - retraction distance (direct drive) for rigid materials : 0.4 mm
  - retraction distance (direct drive) for soft materials : 3 mm

#### Change of stepper motor will require adjustment of Vref for extruder (Default reading Vref 1.19v)
  - Formula for TMC stepper drivers is Vref = `( I * 2.5 ) / Imax`
    - I is the target current value measured in Amps 
    - Imax is 1.77 on regular mode and 1.2 on SilentStepSticks mode
  - Bondtech recommended vref of between .45 - .65

- min vref (0.45 * 2.5) / 1.77 = 0.64
- max vref (0.65 * 2.5) / 1.77 = 0.92
> vref between 0.67v - 0.92v

(0.55 * 2.5) / 1.77 = 0.78v

#### Update Klipper Config to suit Lgx Lite Extruder
  - e-steps value : 562 using 16 microsteps; 1124 using 32 microsteps. 
  - rotation_distance = `full_steps_per_rotation * microsteps / steps_per_mm`
  - rotation_distance = 200 * 16 / 562
  > rotation_distance = 5.7

  - Change extruder direction to suit Lgx-Lite Extruder

**printer.cfg**
```
[extruder] #Driver, Creality Board (TMC2208) (Lgx-Lite Extruder)
dir_pin: PB3  #!PB3 = default direction, PB3 = reverse extruder dimension
```

#### Update Klipper Config to suit new thermister
  - Slice engineering thermister(300)(ATC Semitec 104NT-4-R025H42G)

**printer.cfg**
```
[extruder] #Driver, Creality Board (TMC2208) (Lgx-Lite Extruder)
sensor_type: ATC Semitec 104NT-4-R025H42G
```

  - Calibrate new thermister  
    `PID_CALIBRATE HEATER=extruder TARGET=215`

  - Calibrate new nozzle offset  
    `PROBE_CALIBRATE`

#### 2023_07_19 Input shaping (Resonance Compensation)
  - Check connection to accelerometer in mainsailos  
    `ACCELEROMETER_QUERY`
    
  - Measure axes noise (range ~1-100) (1000+ quality issues)  
    `MEASURE_AXES_NOISE`

  - Measure resonance (per axis)(generates CSV files)  
    `TEST_RESONANCES AXIS=X`  
    `TEST_RESONANCES AXIS=Y`

  - Process generated CSV files (Requires SSH login)  
    `~/klipper/scripts/calibrate_shaper.py /tmp/resonances_x_*.csv -o /tmp/shaper_calibrate_x.png`
    > output:  
    Fitted shaper 'mzv' frequency = 63.2 Hz (vibrations = 0.0%, smoothing ~= 0.051)  
    To avoid too much smoothing with 'mzv', suggested max_accel <= 11800 mm/sec^2

    `~/klipper/scripts/calibrate_shaper.py /tmp/resonances_y_*.csv -o /tmp/shaper_calibrate_y.png`
    > output:  
    Fitted shaper 'mzv' frequency = 45.2 Hz (vibrations = 1.3%, smoothing ~= 0.100)  
    To avoid too much smoothing with 'mzv', suggested max_accel <= 6000 mm/sec^2

  - Update klipper printer.cfg

**printer.cfg**
```
[input_shaper]
shaper_type_x: mzv
shaper_freq_x: 63.2
shaper_type_y: mzv
shaper_freq_y: 45.2

[printer]
max_accel: 10000           #x_max=11800, y_max=6000
```

  - To recalibrate after adjustment (Input Shaper auto-calibration (re-calibration)(does not update max_accel))  
    `SHAPER_CALIBRATE`  
    `SAVE_CONFIG`

#### 2023_08_15 Pressure Advance Tuning
  - 0.4mm nozzle brass

  - Slicer 
    - Set zero infill, and a coarse layer height (the layer height should be around 75% of the nozzle diameter). Make sure any "dynamic acceleration control" is disabled in the slicer.
    - Layer Height: 0.75 * 0.4 = 0.3
    - Layer Width: 1.1 * 0.4 = 0.44
    - Estimated volume: 0.44mm * 0.3mm * 100mm/s = 13.2mm^3/sec

  - Klipper  
    `SET_VELOCITY_LIMIT SQUARE_CORNER_VELOCITY=1 ACCEL=500`  
    `TUNING_TOWER COMMAND=SET_PRESSURE_ADVANCE PARAMETER=ADVANCE START=0 FACTOR=.005`

  - Start tuning tower print

  - Measure print
  - Calculate pressure advance value
    - pressure_advance = `<start> + <measured_height> * <factor>`
    0 + 30 * 0.005 = 0.15
    > pressure_advance = 0.15

  - Update klipper printer.cfg

**printer.cfg**
```
[extruder]
pressure_advance = 0.15
```

----------------------------------------------------------------------------------------------------

## 09_Klipper update RPI(linux)

#### Update Klipper on rpi(raspberry pi) to match updated mcu version
  - 20250125

  - SSH to RPi  
    `ssh pi@<ip_address>`

  - Navigate to Klipper directory  
    `cd ~/klipper/`

  - Klipper configure firmware
    `make menuconfig`

  - change micro-controller architecture to linux process
  - remove !PA15 (possibly still showing from mcu firmware update)

**make menuconfig (CUI)**
```
[*] Enable extra low-level configuration options
    Micro-controller Architecture (Linux proces) --->
() GPIO pins to set at micro-controller startup
```

  - Compile Klipper firmware for rpi
    - Stop Klipper service  
      `sudo service klipper stop`

    - Compile firmware  
      `make flash`

    - Start Klipper service  
      `sudo service klipper start`

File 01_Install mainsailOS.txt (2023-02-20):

Install Mainsail_OS
- Raspberry Pi Imager
  - Choose OS > Other specific-purpose OS > 3D printing > Mainsail OS
    - hostname: mainsail
    - enable ssh
    - user: pi -pwd:
    - configure wireless network

- On Mainsail_OS First Boot
  - wait for file system to expand
  - log in to web interface
    - update components from web interface
      - > settings > machine > Update Manager

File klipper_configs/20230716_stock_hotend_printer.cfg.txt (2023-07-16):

# Klipper Config Creality Ender 7. (stepper motors, 42-60, 1.8 degree, 200 steps)

[include mainsail.cfg]
[include macros.cfg]

[mcu]
#serial: /dev/serial/by-id/usb-1a86_USB_Serial-if00-port0
serial: /dev/ttyUSB0 #sudo dmesg -w
#baud: 115200
restart_method: command

[printer]
kinematics: corexy
max_velocity: 500           #(mm/s) max feedrate (E7:500)(Other:300)
max_accel: 5000             #(mm/s^2)
max_accel_to_decel: 2500    #(mm/s^2) default = half max_accel
square_corner_velocity: 5.0 #(mm/s)
max_z_velocity: 10          #(mm/s) default = max_velocity
max_z_accel: 100            #(mm/s^2) default = max_accel

[stepper_x] #Driver, DM542
step_pin: PC2
dir_pin: PB9
enable_pin: !PC3
rotation_distance: 32
microsteps: 32
full_steps_per_rotation: 200 #1.8=200, 0.9=400
endstop_pin: ^PA5
position_min: 0
position_endstop: 0
position_max: 250
homing_speed: 50

[stepper_y] #Driver, DM542
step_pin: PB8
dir_pin: !PB7
enable_pin: !PC3
rotation_distance: 32
microsteps: 32
full_steps_per_rotation: 200 #1.8=200, 0.9=400
endstop_pin: ^PA6
position_min: 0
position_endstop: 250
position_max: 250
homing_speed: 50

[stepper_z] #Driver, Creality Board (TMC2208)
step_pin: PB6
dir_pin: PB5
enable_pin: !PC3
rotation_distance: 8
microsteps: 16
full_steps_per_rotation: 200         #1.8=200, 0.9=400
#endstop_pin: ^PA7                   # disable to use BLTouch
#position_endstop: 3.0               # disable to use BLTouch
endstop_pin: probe:z_virtual_endstop # enable to use BLTouch
position_min: -4                     # enable to use BLTouch (-3.5)
position_max: 300

[extruder] #Driver, Creality Board (TMC2208)
step_pin: PB4
dir_pin: !PB3
enable_pin: !PC3
microsteps: 16
rotation_distance: 23.564            #
full_steps_per_rotation: 200         #1.8=200
nozzle_diameter: 0.400               #(mm)
filament_diameter: 1.750             #(mm)
max_extrude_cross_section: 2.56      #(mm^2) default = 4.0 * nozzle_diameter^2, (4x0.4=1.6)(1.6^2=2.56)
instantaneous_corner_velocity: 1.000 #(mm/s) default = 1
max_extrude_only_distance: 250.0     #(mm)
#max_extrude_only_velocity:          #(mm/s)
#max_extrude_only_accel:             #(mm/s)^2
#pressure_advance = 0.0              # 0 to disable (original:0.520)
#pressure_advance_smooth_time: 0.040
#HOT END VARIABLES
heater_pin: PA1
max_power: 1.0                      # (0.0-1.0) default:1.0
sensor_type: EPCOS 100K B57560G104F
sensor_pin: PC5
#pullup_resistor: 4700              #default = 4700
#smooth_time: 1.0                   #(s) default = 1
#control: pid                       # tuned for stock hardware with 50 degree Celsius target
#pid_Kp: 19.122                     # PID_CALIBRATE HEATER=extruder TARGET=200
#pid_Ki: 0.898
#pid_Kd: 101.825
min_extrude_temp: 190              #(C) default = 170
min_temp: 1
max_temp: 230

[heater_bed]
heater_pin: PA15
sensor_type: EPCOS 100K B57560G104F
sensor_pin: PC4
#control: pid                       # tuned for stock hardware with 50 degree Celsius target
#pid_Kp: 70.499                     # updated with PID_CALIBRATE HEATER=heater_bed TARGET=60
#pid_Ki: 1.546
#pid_Kd: 803.686
min_temp: 0
max_temp: 75

[fan]
pin: PA0

[filament_switch_sensor filament_sensor]
pause_on_runout: true
switch_pin: !PA4

[bltouch]                    # enable for BLTouch (requires self_test after each firmware restart)
sensor_pin: ^PB1
control_pin: PB0
#z_offset: 2.542             # initial safe value, get correct value by PROBE_CALIBRATE (bltouch: z_offset: 1.904)(bltouch: z_offset: 2.349)(bltouch: z_offset: 2.589)
x_offset: -28.28
y_offset: -28.28
#probe_with_touch_mode: true
pin_move_time: 0.5
#samples: 2
#speed: 2

[safe_z_home]              # BLTouch home x,y axis then move to centre and home z
home_xy_position: 125, 125 # Change coordinates to the center of your print bed
speed: 50
z_hop: 10                  # Move up 10mm
z_hop_speed: 5

[bed_mesh]
speed: 120
horizontal_move_z: 5 #10 #lift z between movements
mesh_min: -25, -25       # x, y (x: 0-28.28=-28.28, -28.28+250= 221.72)
mesh_max: 190, 190
probe_count: 5
#fade_start: 0.6
#fade_end: 10.0
move_check_distance: 5
#mesh_pps: 2,2           #default = 2,2
algorithm: bicubic       #default = lagrange
#bicubic_tension: .2     #default = .2

#Input shaper & resonance tester
[mcu rpi]
serial: /tmp/klipper_host_mcu

[adxl345]
cs_pin: rpi:None

[resonance_tester]
accel_chip: adxl345
probe_points:
    125, 125, 20

[pause_resume] #enable pause_resume
recover_velocity: 50.0 #(mm/s) default = 50.0 mm/s.

#[firmware_retraction] #enable G10 (retract) and G11 (unretract) GCODE commands
#retract_length: 0 #(mm) default = 0
#retract_speed: 20 #(mm/s) default = 20
#unretract_extra_length: 0 #(mm)
#unretract_speed: 10 #(mm/s) deafult = 10

[respond] #Enable the "M118" and "RESPOND" extended commands
default_type: echo #(echo: "echo: "), (command: "// "), (error: "!! ") default = echo
#default_prefix: echo:

#*# <---------------------- SAVE_CONFIG ---------------------->
#*# DO NOT EDIT THIS BLOCK OR BELOW. The contents are auto-generated.
#*#
#*# [bltouch]
#*# z_offset = 2.800
#*#
#*# [bed_mesh default]
#*# version = 1
#*# points =
#*# 	  0.120000, 0.082500, 0.070000, 0.030000, 0.075000
#*# 	  0.072500, 0.027500, 0.022500, 0.002500, 0.037500
#*# 	  0.042500, 0.002500, -0.000000, -0.007500, 0.027500
#*# 	  0.012500, -0.002500, 0.002500, 0.002500, 0.037500
#*# 	  0.007500, 0.015000, 0.042500, 0.045000, 0.065000
#*# x_count = 5
#*# y_count = 5
#*# mesh_x_pps = 2
#*# mesh_y_pps = 2
#*# algo = bicubic
#*# tension = 0.2
#*# min_x = -25.0
#*# max_x = 190.0
#*# min_y = -25.0
#*# max_y = 190.0
#*#
#*# [heater_bed]
#*# control = pid
#*# pid_kp = 74.327
#*# pid_ki = 0.985
#*# pid_kd = 1401.994
#*#
#*# [extruder]
#*# control = pid
#*# pid_kp = 19.588
#*# pid_ki = 1.005
#*# pid_kd = 95.493
#*#
#*# [input_shaper]
#*# shaper_type_x = mzv
#*# shaper_freq_x = 80.0
#*# shaper_type_y = mzv
#*# shaper_freq_y = 61.4
#*#
#*# [bed_mesh 20230701 glass]
#*# version = 1
#*# points =
#*# 	0.102500, 0.070000, 0.057500, 0.012500, 0.042500
#*# 	0.060000, 0.017500, 0.012500, -0.007500, 0.015000
#*# 	0.030000, 0.002500, -0.000000, -0.017500, 0.002500
#*# 	0.005000, -0.000000, 0.010000, -0.000000, 0.025000
#*# 	-0.002500, 0.032500, 0.052500, 0.042500, 0.057500
#*# x_count = 5
#*# y_count = 5
#*# mesh_x_pps = 2
#*# mesh_y_pps = 2
#*# algo = bicubic
#*# tension = 0.2
#*# min_x = -25.0
#*# max_x = 190.0
#*# min_y = -25.0
#*# max_y = 190.0

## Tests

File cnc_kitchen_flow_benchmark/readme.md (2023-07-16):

this folder contains files i used to benchmark my ender-7 using the benchmark test created by cnc kitchen

Links to resources
- https://www.cnckitchen.com/blog/extrusion-system-benchmark-tool-for-fast-prints
- https://github.com/CNCKitchen/ExtrusionSystemBenchmark
- https://hotend-flow-tester.netlify.app/

## Pictures
###### Ender-7 Benchmark Results 2023-07-05 (Hotend: Creality)
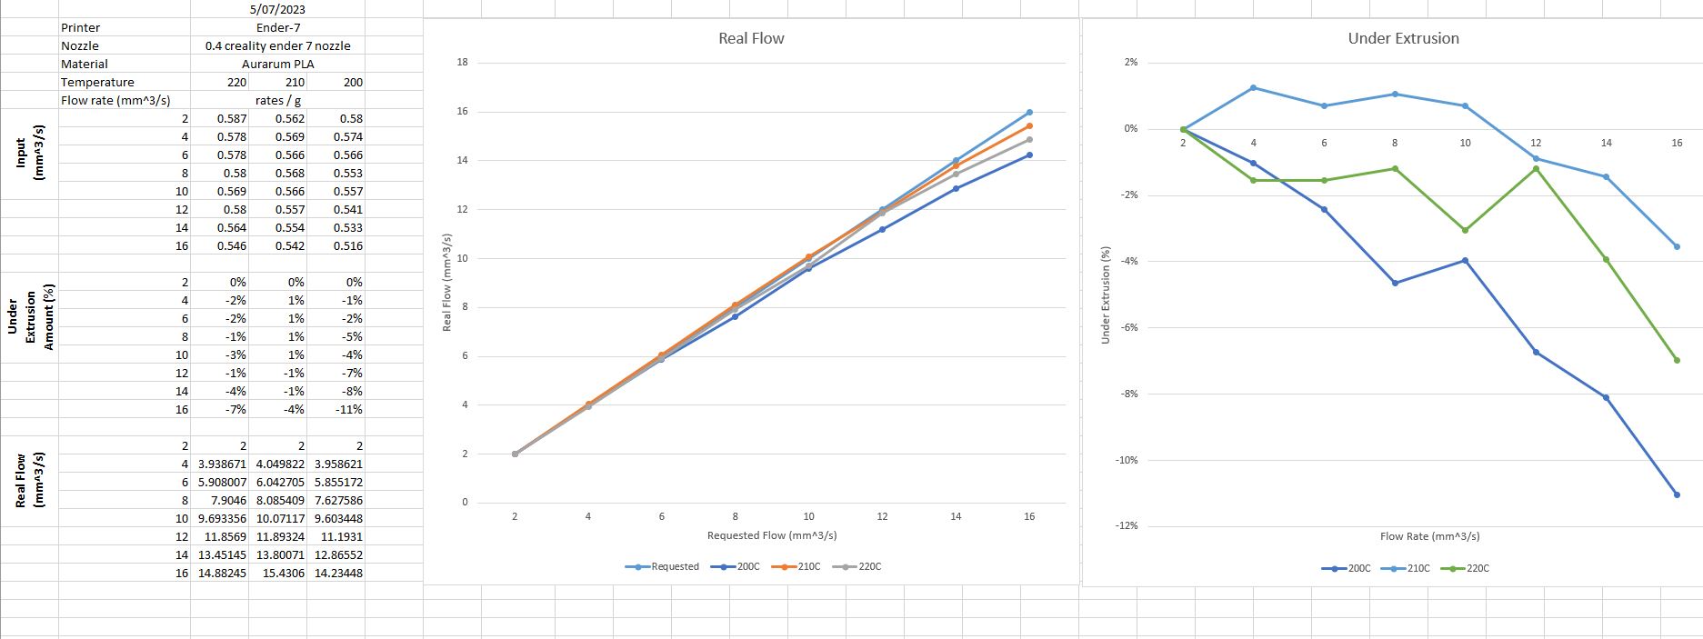
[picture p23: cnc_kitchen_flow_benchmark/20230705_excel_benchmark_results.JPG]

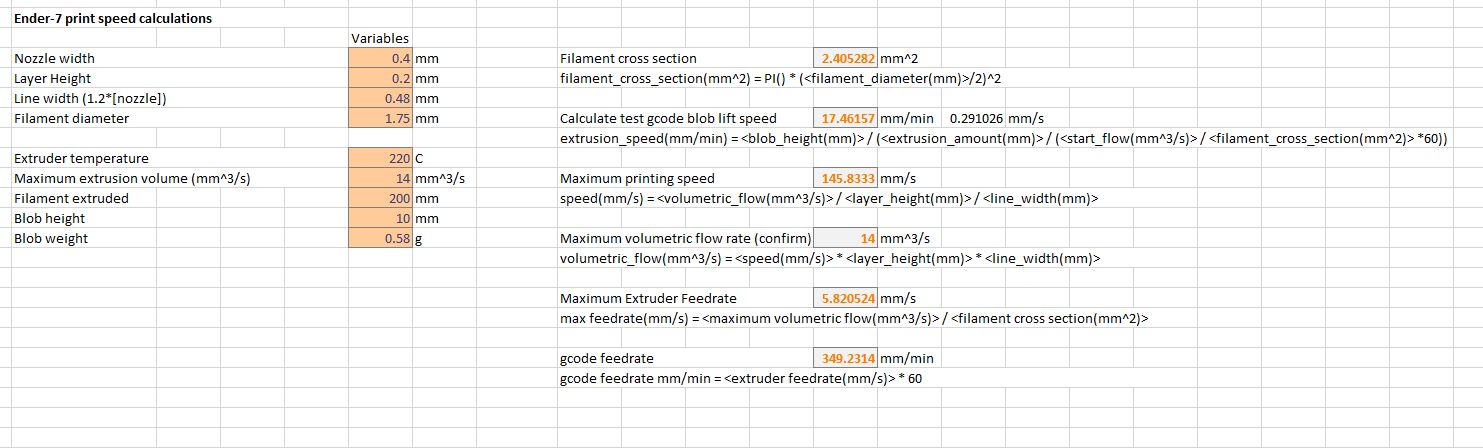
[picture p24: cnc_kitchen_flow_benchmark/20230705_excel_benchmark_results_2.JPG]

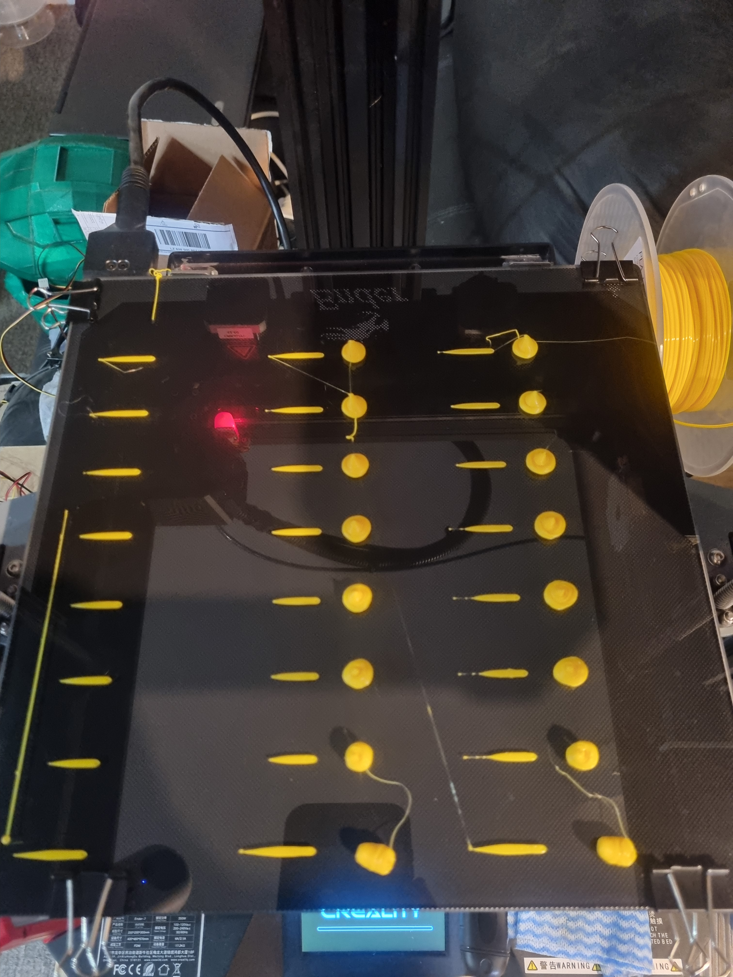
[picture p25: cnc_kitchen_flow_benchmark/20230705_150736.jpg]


20230705 3DBenchy 40min (Top/Bottom Layers,3)(Perminiters,2)(Infill,10%)
Ender-7

## Pictures
###### Ender-7 Benchmark Results 2023-07-05 (Hotend: Mosquito Magnum)
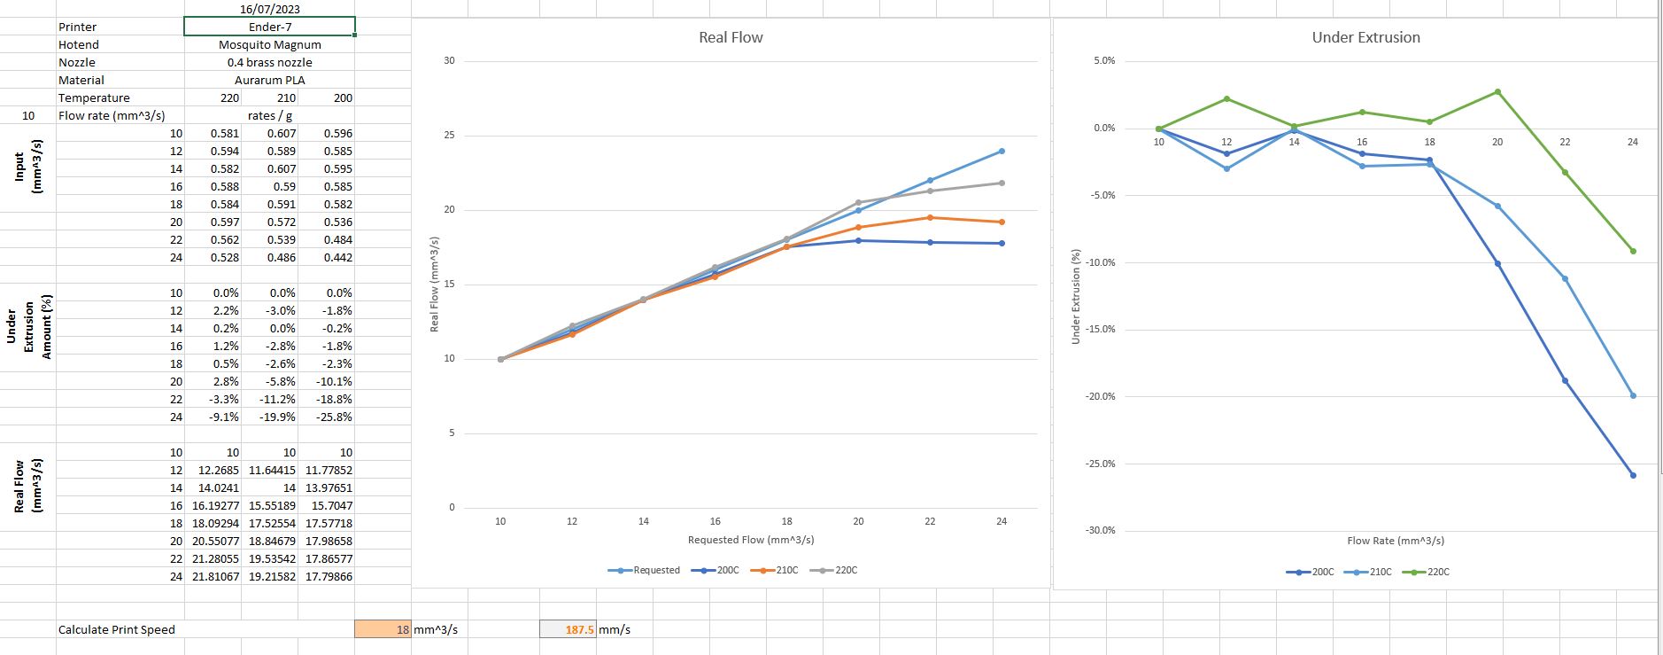
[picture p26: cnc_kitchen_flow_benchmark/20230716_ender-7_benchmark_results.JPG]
Ender-7


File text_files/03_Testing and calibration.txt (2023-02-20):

# Thoroughly test printer (warning can crash printer, be ready to turn of power if somthing goes wrong)

- Checklist
  - Individually check heated bed and hotend temps (set small values and check if temp readings are as expected)
  - Check functionality of all endstops
  - Check homing
  - Check extruder operation(direction)
  - Perform PID tuning for heated bed and hotend
  - Check your extruder is able to extrude the instructed amount of filament 
    - Calibrate e-steps
    - Calibrate flow rate

## Login to MainsailOS web interface and issue commands

### Set heater_bed temp check heat then turn off and check for cool down (safe operation)
  - > SET_HEATER_TEMPERATURE HEATER=heater_bed TARGET=30
  - > SET_HEATER_TEMPERATURE HEATER=heater_bed TARGET=0
  
### Set heater_bed temp check heat then turn off and check for cool down (safe operation)
  - > SET_HEATER_TEMPERATURE HEATER=extruder TARGET=50
  - > SET_HEATER_TEMPERATURE HEATER=extruder TARGET=0
  
### Check endstops operation (with BLTouch)
  - Disable motors
    - > M83
  - Manually move print head away from end stops to center
  - Manually lower print bed out of way
  
  - Check endstops status
    - > QUERY_ENDSTOPS
      - return: x:open y:open z:open
  - Manually press and hold each endstop switch (X,Y) and check operation
    - > QUERY_ENDSTOPS
      - return: x:triggered y:triggered z:open
  
  - Test BLTouch operation (Z axis)
    - > bltouch_debug command=pin_down      # pin goes down, light goes off
    - > bltouch_debug command=pin_up        # pin goes up, red light goes on
    
  - Test BLTouch Z endstop operation
    - > bltouch_debug command=pin_down
    - > bltouch_debug command=touch_mode
    - > query_probe
      - return: probe: open
    - Slightly press and hold bltouch probe so it lights up but does not fully retract and query
      - > query_probe
        - return: probe: triggered
      - > QUERY_ENDSTOPS
        - return: x:open y:open z:triggered
    - If probe blinks (probe state error)
      - > bltouch_debug command=reset        # reset probe if fault(blinking)
      - > bltouch_debug command=self_test    # pin goes down and up repeatedly, red light stays on
      
### Check Homing
  - Verify stepper motor operation (Move axis 1mm back and forth 10 times)
    - > STEPPER_BUZZ STEPPER=stepper_x
    - > STEPPER_BUZZ STEPPER=stepper_y
    - > STEPPER_BUZZ STEPPER=stepper_z
    
  - Verify direction and homeing(endstop) per axis
    - Home X axis
      - > G28 x
    - Home Y axis
      - > G28 y
    - Home Z axis (Probe should drop first then bed will start moving)
      - > G28 z
  
### Calibrate Z offset
  - > probe_calibrate
    - Adjust z-offset (Peice of paper just dragging between nozzle and bed)
      - > testz=-0.1
      - > testz=+0.1
    - When happy with adjustment enter accept command in console
      - > accept
    
  - Verify accuracy of Z offset
    - > probe_accuracy
      - 0.0125 or better, 0.025 no worse
      - return: standard deviation of 0.002077
      
### Check extruder operation (direction) (no filament)
  - Set E to relative
    - > M83
  - Extrude 100mm
    - > G1 E100 F100
  - Retract 100mm
    - > G1 E-100 F100
    
### Perform PID tuning for heated bed and hotend (feed in filament so hotend is not empty for test)
  - > PID_CALIBRATE HEATER=heater_bed TARGET=60
    - return: PID parameters: pid_Kp=74.515 pid_Ki=1.153 pid_Kd=1204.353
    
  - > PID_CALIBRATE HEATER=extruder TARGET=200
    - return: PID parameters: pid_Kp=21.862 pid_Ki=1.139 pid_Kd=104.939
    
  - When PID tuning complete save
    - > save_config
    
### Calibrate Extruder (Calibrate e-steps) (Klipper: rotation_distance)
  - [Method_1] Obtaining rotation_distance from steps_per_mm (e-steps)(approximation)
    - Retrieve e-steps from firmware (Marlin) before flashing microcontroller with Klipper
      - > M503
        - return: M92 X200.00 Y200.00 Z400.00 E140.00
        - 140 e-steps
    - Calculate rotation distance
      - rotation_distance = <full_steps_per_rotation> * <microsteps> / <steps_per_mm>
        - 1.8 degree motor (full rotation = 200 steps (360/1.8=200))
        - 16 microsteps
        - 200 * 16 / 140 = 22.857
      - rotation_distance = 22.857mm
  
  - [Method_2] Obtaining rotation_distance from measure and trim
    - Heat extruder to 210C with filament
    - Mark Filament at 100mm from intake to extruder
    - Mark Filament at 120mm from intake to extruder
    - Extrude 100mm filament (low speed minimul pressure in extruder)
      - Set Extruder relative
        - > G91
      - Extrude 100mm
        - > G1 E100 F100
    - Measure remaining distance to mark (120mm mark to beginning of extruder)
      - Remaining Measurement = 23mm
    - actual_extrude_distance = <initial_mark_distance> - <subsequent_mark_distance>
      - 120 - 23 = 97mm
    - Previous e-steps
      - 140 e-steps / 100mm = 1.4 step per mm
    - Current e-steps
      - Actual length extruded = 120mm – (Length from the extruder to mark after extruding)
        - 120mm - 23mm = 97mm
      - Accurate steps/mm = (Old steps/mm × Actual length extruded)
        - 1.4steps/mm * 97mm = 135.8steps/mm
    - New rotation_distance for Klipper
      - rotation_distance = <full_steps_per_rotation> * <microsteps> / <steps_per_mm>
        - 200steps * (16microsteps / 135.8steps/mm) = 23.564mm
        
### Calibrate flow rate (specific to each filament)
  - PrusaSlicer (extrusion multiplier)
  - Create/download a flow rate calibration model (50mm solid cube) and slice
    - Slicer print settings:
      - Layer Height: 0.2mm (or set to your normal printer layer height)
        - PrusaSlicer > print settings > layers and perimeters > Layer height
      -Line Width: 0.4 (wall thickness)
        - PrusaSlicer > print settings > advanced > default extrusion width
      -Wall Count(Perimeters): 1
        - PrusaSlicer > print settings > layers and perimeters > Perimeters
      -Infill Density: Set to 0%
      -Top layers: set to 0 to make cube hollow
        - PrusaSlicer > print settings > layers and perimeters > Solid layers > Top
      -Print Speed: Set to your normal wall printing speed
        - PrusaSlicer > print settings > layers and perimeters > Perimeters (default 40mm/s)
    - Slicer filament settings
      - PrusaSlicer Generic PLA
        - Nozzle, First Layer:215C, Other Layers:215C
        - Bed,    First Layer:60C,  Other Layers:60C

  - Print Model with settings above
  
  - Measure each wall thickness at center on print with calipers
    - measurements: 0.36, 0.4, 0.39, 0.35
    - 0.36 + 0.4 + 0.39 + 0.35 = 1.5mm
    - 1.5 / 4 = 0.375mm average wall thickness
    
  - Calculate flow rate
    - New flow rate (%) = (0.4 ÷ average wall width) × 100
    - (0.4 / 0.375) * 100 = 106.667%
    - Extrusion Multiplier: 106.667% = 1.07
  
  - Update PrusaSlicer Extrusion Multiplier (recommended range: 0.9-1.1)
    - Filament Settings > Filament > Extrusion multiplier = 1.07

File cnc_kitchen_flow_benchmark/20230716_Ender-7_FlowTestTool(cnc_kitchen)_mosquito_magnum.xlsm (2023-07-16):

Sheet: Settings
General Settings |  |  | Created by CNC Kitchen
Bed Width | 250 | mm
Bed Length | 250 | mm
Bed Margin | 5 | mm
Filament Diameter | 1.75 | mm
Travel Speed | 100 | mm/s
Stabilization Time | 20 | s
Bed Temperature | 60 | °C
Fan Speed | 0 | %
Prime Length | 25 | mm
Prime Amount | 20 | mm | Prime Flow
Prime Speed | 5 | mm/s | 9.621127502 | mm³/s
Wipe Length | 15 | mm
Retraction Distance | 1 | mm
Retraction Speed | 35 | mm/s
Blob Height | 10 | mm
Extrusion Amount | 200 | mm
Direction | 1 | 1=front to back, -1=back to front
Temperature Spacing | 45 | mm
Flow Spacing | 30 | mm
DOE Settings
Flow Variation
Start Flow | 10 | mm³/s
Offset | 2 | mm³/s
Steps | 8
End Flow | 24 | mm³/s | 24mm^3 = 250mm/s
Temperature Variation
Start Temperature | 220 | °C
Offset | 10 | K
Steps | 3 |  | If Steps = 1 "Fill Mode" is used
End Flow | 200 | °C
Comment | Ender-7
total bed width required | 220 | OK
total bed length required | 250 | OK

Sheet: Output
; *** CNC Kitchen Auto Flow Pattern Generator 0.93
;Adapted for klipper
;####### Settings
; Ender-7
; bedWidth = 250
; bedLength = 250
; bedMargin = 5
; filamentDiameter = 1.75
; movementSpeed = 100
; stabilizationTime = 20
; bedTemp = 60
; primeLength = 25
; primeAmount = 20
; primeSpeed = 5
; retractionDistance = 1
; retractionSpeed = 35
; blobHeight = 10
; extrusionAmount = 200
; xSpacing = 45
; ySpacing = 30
; startFlow = 10
; flowOffset = 2
; flowSteps = 8
; startTemp = 220
; tempOffset = 10
; tempSteps = 3
; direction = 1
;E7 Klipper start macro
PRINT_START
M104 S200
M140 S60
;[SAFETY] Force Relative Extrusion
M83 ; set extruder to relative mode
;####### 220C
G4 S0 ; Dwell
M109 S220
;####### 10mm3/s
M117 220°C // 10mm3/s
G0 X5 Y5 Z15.5 F6000
G4 S20; Stabalize
G0 Z0.3 ; Drop down
G1 X30 E20 F300 ;Prime
G1 E-1 F2100; Retract
G0 X45 F6000 ; Wipe
G0 Z0.5 ; Lift
G1 E1 F2100 ; De-Retract
G1 Z10.5 E200 F12.47 ; Extrude
G1 E-1 F2100 ; Retract
G0 Z15.5; Lift
G0 X5 Y5 F6000
G92 E0 ; Reset Extruder
;####### 12mm3/s
M117 220°C // 12mm3/s
G0 X5 Y35 Z15.5 F6000
G4 S20; Stabalize
G0 Z0.3 ; Drop down
G1 X30 E20 F300 ;Prime
G1 E-1 F2100; Retract
G0 X45 F6000 ; Wipe
G0 Z0.5 ; Lift
G1 E1 F2100 ; De-Retract
G1 Z10.5 E200 F14.97 ; Extrude
G1 E-1 F2100 ; Retract
G0 Z15.5; Lift
G0 X5 Y35 F6000
G92 E0 ; Reset Extruder
;####### 14mm3/s
M117 220°C // 14mm3/s
G0 X5 Y65 Z15.5 F6000
G4 S20; Stabalize
G0 Z0.3 ; Drop down
G1 X30 E20 F300 ;Prime
G1 E-1 F2100; Retract
G0 X45 F6000 ; Wipe
G0 Z0.5 ; Lift
G1 E1 F2100 ; De-Retract
G1 Z10.5 E200 F17.46 ; Extrude
G1 E-1 F2100 ; Retract
G0 Z15.5; Lift
G0 X5 Y65 F6000
G92 E0 ; Reset Extruder
;####### 16mm3/s
M117 220°C // 16mm3/s
G0 X5 Y95 Z15.5 F6000
G4 S20; Stabalize
G0 Z0.3 ; Drop down
G1 X30 E20 F300 ;Prime
G1 E-1 F2100; Retract
G0 X45 F6000 ; Wipe
G0 Z0.5 ; Lift
G1 E1 F2100 ; De-Retract
G1 Z10.5 E200 F19.96 ; Extrude
G1 E-1 F2100 ; Retract
G0 Z15.5; Lift
G0 X5 Y95 F6000
G92 E0 ; Reset Extruder
;####### 18mm3/s
M117 220°C // 18mm3/s
G0 X5 Y125 Z15.5 F6000
G4 S20; Stabalize
G0 Z0.3 ; Drop down
G1 X30 E20 F300 ;Prime
G1 E-1 F2100; Retract
G0 X45 F6000 ; Wipe
G0 Z0.5 ; Lift
G1 E1 F2100 ; De-Retract
G1 Z10.5 E200 F22.45 ; Extrude
G1 E-1 F2100 ; Retract
G0 Z15.5; Lift
G0 X5 Y125 F6000
G92 E0 ; Reset Extruder
;####### 20mm3/s
M117 220°C // 20mm3/s
G0 X5 Y155 Z15.5 F6000
G4 S20; Stabalize
G0 Z0.3 ; Drop down
G1 X30 E20 F300 ;Prime
G1 E-1 F2100; Retract
G0 X45 F6000 ; Wipe
G0 Z0.5 ; Lift
G1 E1 F2100 ; De-Retract
G1 Z10.5 E200 F24.95 ; Extrude
G1 E-1 F2100 ; Retract
G0 Z15.5; Lift
G0 X5 Y155 F6000
G92 E0 ; Reset Extruder
;####### 22mm3/s
M117 220°C // 22mm3/s
G0 X5 Y185 Z15.5 F6000
G4 S20; Stabalize
G0 Z0.3 ; Drop down
G1 X30 E20 F300 ;Prime
G1 E-1 F2100; Retract
G0 X45 F6000 ; Wipe
G0 Z0.5 ; Lift
G1 E1 F2100 ; De-Retract
G1 Z10.5 E200 F27.44 ; Extrude
G1 E-1 F2100 ; Retract
G0 Z15.5; Lift
G0 X5 Y185 F6000
G92 E0 ; Reset Extruder
;####### 24mm3/s
M117 220°C // 24mm3/s
G0 X5 Y215 Z15.5 F6000
G4 S20; Stabalize
G0 Z0.3 ; Drop down
G1 X30 E20 F300 ;Prime
G1 E-1 F2100; Retract
G0 X45 F6000 ; Wipe
G0 Z0.5 ; Lift
G1 E1 F2100 ; De-Retract
G1 Z10.5 E200 F29.93 ; Extrude
G1 E-1 F2100 ; Retract
G0 Z15.5; Lift
G0 X5 Y215 F6000
G92 E0 ; Reset Extruder
;####### 210C
G4 S0 ; Dwell
M109 S210
;####### 10mm3/s
M117 210°C // 10mm3/s
G0 X90 Y5 Z15.5 F6000
G4 S20; Stabalize
G0 Z0.3 ; Drop down
G1 X115 E20 F300 ;Prime
G1 E-1 F2100; Retract
G0 X130 F6000 ; Wipe
G0 Z0.5 ; Lift
G1 E1 F2100 ; De-Retract
G1 Z10.5 E200 F12.47 ; Extrude
G1 E-1 F2100 ; Retract
G0 Z15.5; Lift
G0 X90 Y5 F6000
G92 E0 ; Reset Extruder
;####### 12mm3/s
M117 210°C // 12mm3/s
G0 X90 Y35 Z15.5 F6000
G4 S20; Stabalize
G0 Z0.3 ; Drop down
G1 X115 E20 F300 ;Prime
G1 E-1 F2100; Retract
G0 X130 F6000 ; Wipe
G0 Z0.5 ; Lift
G1 E1 F2100 ; De-Retract
G1 Z10.5 E200 F14.97 ; Extrude
G1 E-1 F2100 ; Retract
G0 Z15.5; Lift
G0 X90 Y35 F6000
G92 E0 ; Reset Extruder
;####### 14mm3/s
M117 210°C // 14mm3/s
G0 X90 Y65 Z15.5 F6000
G4 S20; Stabalize
G0 Z0.3 ; Drop down
G1 X115 E20 F300 ;Prime
G1 E-1 F2100; Retract
G0 X130 F6000 ; Wipe
G0 Z0.5 ; Lift
G1 E1 F2100 ; De-Retract
G1 Z10.5 E200 F17.46 ; Extrude
G1 E-1 F2100 ; Retract
G0 Z15.5; Lift
G0 X90 Y65 F6000
G92 E0 ; Reset Extruder
;####### 16mm3/s
M117 210°C // 16mm3/s
G0 X90 Y95 Z15.5 F6000
G4 S20; Stabalize
G0 Z0.3 ; Drop down
G1 X115 E20 F300 ;Prime
G1 E-1 F2100; Retract
G0 X130 F6000 ; Wipe
G0 Z0.5 ; Lift
G1 E1 F2100 ; De-Retract
G1 Z10.5 E200 F19.96 ; Extrude
G1 E-1 F2100 ; Retract
G0 Z15.5; Lift
G0 X90 Y95 F6000
G92 E0 ; Reset Extruder
;####### 18mm3/s
M117 210°C // 18mm3/s
G0 X90 Y125 Z15.5 F6000
G4 S20; Stabalize
G0 Z0.3 ; Drop down
G1 X115 E20 F300 ;Prime
G1 E-1 F2100; Retract
G0 X130 F6000 ; Wipe
G0 Z0.5 ; Lift
G1 E1 F2100 ; De-Retract
G1 Z10.5 E200 F22.45 ; Extrude
G1 E-1 F2100 ; Retract
G0 Z15.5; Lift
G0 X90 Y125 F6000
G92 E0 ; Reset Extruder
;####### 20mm3/s
M117 210°C // 20mm3/s
G0 X90 Y155 Z15.5 F6000
G4 S20; Stabalize
G0 Z0.3 ; Drop down
G1 X115 E20 F300 ;Prime
G1 E-1 F2100; Retract
G0 X130 F6000 ; Wipe
G0 Z0.5 ; Lift
G1 E1 F2100 ; De-Retract
G1 Z10.5 E200 F24.95 ; Extrude
G1 E-1 F2100 ; Retract
G0 Z15.5; Lift
G0 X90 Y155 F6000
G92 E0 ; Reset Extruder
;####### 22mm3/s
M117 210°C // 22mm3/s
G0 X90 Y185 Z15.5 F6000
G4 S20; Stabalize
G0 Z0.3 ; Drop down
G1 X115 E20 F300 ;Prime
G1 E-1 F2100; Retract
G0 X130 F6000 ; Wipe
G0 Z0.5 ; Lift
G1 E1 F2100 ; De-Retract
G1 Z10.5 E200 F27.44 ; Extrude
G1 E-1 F2100 ; Retract
G0 Z15.5; Lift
G0 X90 Y185 F6000
G92 E0 ; Reset Extruder
;####### 24mm3/s
M117 210°C // 24mm3/s
G0 X90 Y215 Z15.5 F6000
G4 S20; Stabalize
G0 Z0.3 ; Drop down
G1 X115 E20 F300 ;Prime
G1 E-1 F2100; Retract
G0 X130 F6000 ; Wipe
G0 Z0.5 ; Lift
G1 E1 F2100 ; De-Retract
G1 Z10.5 E200 F29.93 ; Extrude
G1 E-1 F2100 ; Retract
G0 Z15.5; Lift
G0 X90 Y215 F6000
G92 E0 ; Reset Extruder
;####### 200C
G4 S0 ; Dwell
M109 S200
;####### 10mm3/s
M117 200°C // 10mm3/s
G0 X175 Y5 Z15.5 F6000
G4 S20; Stabalize
G0 Z0.3 ; Drop down
G1 X200 E20 F300 ;Prime
G1 E-1 F2100; Retract
G0 X215 F6000 ; Wipe
G0 Z0.5 ; Lift
G1 E1 F2100 ; De-Retract
G1 Z10.5 E200 F12.47 ; Extrude
G1 E-1 F2100 ; Retract
G0 Z15.5; Lift
G0 X175 Y5 F6000
G92 E0 ; Reset Extruder
;####### 12mm3/s
M117 200°C // 12mm3/s
G0 X175 Y35 Z15.5 F6000
G4 S20; Stabalize
G0 Z0.3 ; Drop down
G1 X200 E20 F300 ;Prime
G1 E-1 F2100; Retract
G0 X215 F6000 ; Wipe
G0 Z0.5 ; Lift
G1 E1 F2100 ; De-Retract
G1 Z10.5 E200 F14.97 ; Extrude
G1 E-1 F2100 ; Retract
G0 Z15.5; Lift
G0 X175 Y35 F6000
G92 E0 ; Reset Extruder
;####### 14mm3/s
M117 200°C // 14mm3/s
G0 X175 Y65 Z15.5 F6000
G4 S20; Stabalize
G0 Z0.3 ; Drop down
G1 X200 E20 F300 ;Prime
G1 E-1 F2100; Retract
G0 X215 F6000 ; Wipe
G0 Z0.5 ; Lift
G1 E1 F2100 ; De-Retract
G1 Z10.5 E200 F17.46 ; Extrude
G1 E-1 F2100 ; Retract
G0 Z15.5; Lift
G0 X175 Y65 F6000
G92 E0 ; Reset Extruder
;####### 16mm3/s
M117 200°C // 16mm3/s
G0 X175 Y95 Z15.5 F6000
G4 S20; Stabalize
G0 Z0.3 ; Drop down
G1 X200 E20 F300 ;Prime
G1 E-1 F2100; Retract
G0 X215 F6000 ; Wipe
G0 Z0.5 ; Lift
G1 E1 F2100 ; De-Retract
G1 Z10.5 E200 F19.96 ; Extrude
G1 E-1 F2100 ; Retract
G0 Z15.5; Lift
G0 X175 Y95 F6000
G92 E0 ; Reset Extruder
;####### 18mm3/s
M117 200°C // 18mm3/s
G0 X175 Y125 Z15.5 F6000
G4 S20; Stabalize
G0 Z0.3 ; Drop down
G1 X200 E20 F300 ;Prime
G1 E-1 F2100; Retract
G0 X215 F6000 ; Wipe
G0 Z0.5 ; Lift
G1 E1 F2100 ; De-Retract
G1 Z10.5 E200 F22.45 ; Extrude
G1 E-1 F2100 ; Retract
G0 Z15.5; Lift
G0 X175 Y125 F6000
G92 E0 ; Reset Extruder
;####### 20mm3/s
M117 200°C // 20mm3/s
G0 X175 Y155 Z15.5 F6000
G4 S20; Stabalize
G0 Z0.3 ; Drop down
G1 X200 E20 F300 ;Prime
G1 E-1 F2100; Retract
G0 X215 F6000 ; Wipe
G0 Z0.5 ; Lift
G1 E1 F2100 ; De-Retract
G1 Z10.5 E200 F24.95 ; Extrude
G1 E-1 F2100 ; Retract
G0 Z15.5; Lift
G0 X175 Y155 F6000
G92 E0 ; Reset Extruder
;####### 22mm3/s
M117 200°C // 22mm3/s
G0 X175 Y185 Z15.5 F6000
G4 S20; Stabalize
G0 Z0.3 ; Drop down
G1 X200 E20 F300 ;Prime
G1 E-1 F2100; Retract
G0 X215 F6000 ; Wipe
G0 Z0.5 ; Lift
G1 E1 F2100 ; De-Retract
G1 Z10.5 E200 F27.44 ; Extrude
G1 E-1 F2100 ; Retract
G0 Z15.5; Lift
G0 X175 Y185 F6000
G92 E0 ; Reset Extruder
;####### 24mm3/s
M117 200°C // 24mm3/s
G0 X175 Y215 Z15.5 F6000
G4 S20; Stabalize
G0 Z0.3 ; Drop down
G1 X200 E20 F300 ;Prime
G1 E-1 F2100; Retract
G0 X215 F6000 ; Wipe
G0 Z0.5 ; Lift
G1 E1 F2100 ; De-Retract
G1 Z10.5 E200 F29.93 ; Extrude
G1 E-1 F2100 ; Retract
G0 Z15.5; Lift
G0 X175 Y215 F6000
G92 E0 ; Reset Extruder
;####### End G-Code
PRINT_STOP

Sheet: SampleEvaluation
 |  | Test 1
 | Printer | Ender-7 Pro
 | Material | Filament PLA
 | Temperature / °C | 220 | 210 | 200
 | Flow rate / mm³/s | weights / g
Input | 10 | 0.581 | 0.607 | 0.596
 | 12 | 0.594 | 0.589 | 0.585
 | 14 | 0.582 | 0.607 | 0.595
 | 16 | 0.588 | 0.59 | 0.585
 | 18 | 0.584 | 0.591 | 0.582
 | 20 | 0.597 | 0.572 | 0.536
 | 22 | 0.562 | 0.539 | 0.484
 | 24 | 0.528 | 0.486 | 0.442
Underextrusion Amount | 10 | 0% | 0% | 0%
 | 12 | 2.237521515% | -2.965403624% | -1.845637584%
 | 14 | 0.1721170396% | 0% | -0.1677852349%
 | 16 | 1.204819277% | -2.800658979% | -1.845637584%
 | 18 | 0.5163511188% | -2.635914333% | -2.348993289%
 | 20 | 2.753872633% | -5.766062603% | -10.06711409%
 | 22 | -3.270223752% | -11.20263591% | -18.79194631%
 | 24 | -9.122203098% | -19.93410214% | -25.83892617%
Real Flow | 10 | 10.0 | 10.0 | 10.0
 | 12 | 12.3 | 11.6 | 11.8
 | 14 | 14.0 | 14.0 | 14.0
 | 16 | 16.2 | 15.6 | 15.7
 | 18 | 18.1 | 17.5 | 17.6
 | 20 | 20.6 | 18.8 | 18.0
 | 22 | 21.3 | 19.5 | 17.9
 | 24 | 21.8 | 19.2 | 17.8
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

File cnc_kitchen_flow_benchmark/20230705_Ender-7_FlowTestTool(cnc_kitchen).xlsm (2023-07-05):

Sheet: Settings
General Settings |  |  | Created by CNC Kitchen
Bed Width | 250 | mm
Bed Length | 250 | mm
Bed Margin | 5 | mm
Filament Diameter | 1.75 | mm
Travel Speed | 100 | mm/s
Stabilization Time | 20 | s
Bed Temperature | 60 | °C
Fan Speed | 0 | %
Prime Length | 25 | mm
Prime Amount | 20 | mm | Prime Flow
Prime Speed | 5 | mm/s | 9.621127502 | mm³/s
Wipe Length | 15 | mm
Retraction Distance | 8 | mm
Retraction Speed | 60 | mm/s
Blob Height | 10 | mm
Extrusion Amount | 200 | mm
Direction | 1 | 1=front to back, -1=back to front
Temperature Spacing | 40 | mm
Flow Spacing | 30 | mm
DOE Settings
Flow Variation
Start Flow | 2 | mm³/s
Offset | 2 | mm³/s
Steps | 8
End Flow | 16 | mm³/s
Temperature Variation
Start Temperature | 220 | °C
Offset | 10 | K
Steps | 3 |  | If Steps = 1 "Fill Mode" is used
End Flow | 200 | °C
Comment | Ender-7
total bed width required | 210 | OK
total bed length required | 250 | OK

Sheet: Output
; *** CNC Kitchen Auto Flow Pattern Generator 0.93
; *** 02/04/26 Stefan Hermann
;####### Settings
; Ender-7
; bedWidth = 250
; bedLength = 250
; bedMargin = 5
; filamentDiameter = 1.75
; movementSpeed = 100
; stabilizationTime = 20
; bedTemp = 60
; primeLength = 25
; primeAmount = 20
; primeSpeed = 5
; retractionDistance = 8
; retractionSpeed = 60
; blobHeight = 10
; extrusionAmount = 200
; xSpacing = 40
; ySpacing = 30
; startFlow = 2
; flowOffset = 2
; flowSteps = 8
; startTemp = 220
; tempOffset = 10
; tempSteps = 3
; direction = 1
M104 S220 ; Set Nozzle Temperature
M140 S60 ; Set Bed Temperature
G90
G28 ; Move to home position
G0 Z10 ; Lift nozzle
G21; unit in mm
G92 E0; reset extruder
M83; set extruder to relative mode
M190 S60 ; Set Bed Temperature & Wait
M106 S0 ; Set Fan Speed
;####### 220C
G4 S0 ; Dwell
M109 S220
;####### 2mm3/s
M117 220°C // 2mm3/s
G0 X5 Y5 Z15.5 F6000
G4 S20; Stabalize
G0 Z0.3 ; Drop down
G1 X30 E20 F300 ;Prime
G1 E-8 F3600; Retract
G0 X45 F6000 ; Wipe
G0 Z0.5 ; Lift
G1 E8 F3600 ; De-Retract
G1 Z10.5 E200 F2.49 ; Extrude
G1 E-8 F3600 ; Retract
G0 Z15.5; Lift
G0 X5 Y5 F6000
G92 E0 ; Reset Extruder
;####### 4mm3/s
M117 220°C // 4mm3/s
G0 X5 Y35 Z15.5 F6000
G4 S20; Stabalize
G0 Z0.3 ; Drop down
G1 X30 E20 F300 ;Prime
G1 E-8 F3600; Retract
G0 X45 F6000 ; Wipe
G0 Z0.5 ; Lift
G1 E8 F3600 ; De-Retract
G1 Z10.5 E200 F4.99 ; Extrude
G1 E-8 F3600 ; Retract
G0 Z15.5; Lift
G0 X5 Y35 F6000
G92 E0 ; Reset Extruder
;####### 6mm3/s
M117 220°C // 6mm3/s
G0 X5 Y65 Z15.5 F6000
G4 S20; Stabalize
G0 Z0.3 ; Drop down
G1 X30 E20 F300 ;Prime
G1 E-8 F3600; Retract
G0 X45 F6000 ; Wipe
G0 Z0.5 ; Lift
G1 E8 F3600 ; De-Retract
G1 Z10.5 E200 F7.48 ; Extrude
G1 E-8 F3600 ; Retract
G0 Z15.5; Lift
G0 X5 Y65 F6000
G92 E0 ; Reset Extruder
;####### 8mm3/s
M117 220°C // 8mm3/s
G0 X5 Y95 Z15.5 F6000
G4 S20; Stabalize
G0 Z0.3 ; Drop down
G1 X30 E20 F300 ;Prime
G1 E-8 F3600; Retract
G0 X45 F6000 ; Wipe
G0 Z0.5 ; Lift
G1 E8 F3600 ; De-Retract
G1 Z10.5 E200 F9.98 ; Extrude
G1 E-8 F3600 ; Retract
G0 Z15.5; Lift
G0 X5 Y95 F6000
G92 E0 ; Reset Extruder
;####### 10mm3/s
M117 220°C // 10mm3/s
G0 X5 Y125 Z15.5 F6000
G4 S20; Stabalize
G0 Z0.3 ; Drop down
G1 X30 E20 F300 ;Prime
G1 E-8 F3600; Retract
G0 X45 F6000 ; Wipe
G0 Z0.5 ; Lift
G1 E8 F3600 ; De-Retract
G1 Z10.5 E200 F12.47 ; Extrude
G1 E-8 F3600 ; Retract
G0 Z15.5; Lift
G0 X5 Y125 F6000
G92 E0 ; Reset Extruder
;####### 12mm3/s
M117 220°C // 12mm3/s
G0 X5 Y155 Z15.5 F6000
G4 S20; Stabalize
G0 Z0.3 ; Drop down
G1 X30 E20 F300 ;Prime
G1 E-8 F3600; Retract
G0 X45 F6000 ; Wipe
G0 Z0.5 ; Lift
G1 E8 F3600 ; De-Retract
G1 Z10.5 E200 F14.97 ; Extrude
G1 E-8 F3600 ; Retract
G0 Z15.5; Lift
G0 X5 Y155 F6000
G92 E0 ; Reset Extruder
;####### 14mm3/s
M117 220°C // 14mm3/s
G0 X5 Y185 Z15.5 F6000
G4 S20; Stabalize
G0 Z0.3 ; Drop down
G1 X30 E20 F300 ;Prime
G1 E-8 F3600; Retract
G0 X45 F6000 ; Wipe
G0 Z0.5 ; Lift
G1 E8 F3600 ; De-Retract
G1 Z10.5 E200 F17.46 ; Extrude
G1 E-8 F3600 ; Retract
G0 Z15.5; Lift
G0 X5 Y185 F6000
G92 E0 ; Reset Extruder
;####### 16mm3/s
M117 220°C // 16mm3/s
G0 X5 Y215 Z15.5 F6000
G4 S20; Stabalize
G0 Z0.3 ; Drop down
G1 X30 E20 F300 ;Prime
G1 E-8 F3600; Retract
G0 X45 F6000 ; Wipe
G0 Z0.5 ; Lift
G1 E8 F3600 ; De-Retract
G1 Z10.5 E200 F19.96 ; Extrude
G1 E-8 F3600 ; Retract
G0 Z15.5; Lift
G0 X5 Y215 F6000
G92 E0 ; Reset Extruder
;####### 230C
G4 S0 ; Dwell
M109 S230
;####### 2mm3/s
M117 210°C // 2mm3/s
G0 X85 Y5 Z15.5 F6000
G4 S20; Stabalize
G0 Z0.3 ; Drop down
G1 X110 E20 F300 ;Prime
G1 E-8 F3600; Retract
G0 X125 F6000 ; Wipe
G0 Z0.5 ; Lift
G1 E8 F3600 ; De-Retract
G1 Z10.5 E200 F2.49 ; Extrude
G1 E-8 F3600 ; Retract
G0 Z15.5; Lift
G0 X85 Y5 F6000
G92 E0 ; Reset Extruder
;####### 4mm3/s
M117 210°C // 4mm3/s
G0 X85 Y35 Z15.5 F6000
G4 S20; Stabalize
G0 Z0.3 ; Drop down
G1 X110 E20 F300 ;Prime
G1 E-8 F3600; Retract
G0 X125 F6000 ; Wipe
G0 Z0.5 ; Lift
G1 E8 F3600 ; De-Retract
G1 Z10.5 E200 F4.99 ; Extrude
G1 E-8 F3600 ; Retract
G0 Z15.5; Lift
G0 X85 Y35 F6000
G92 E0 ; Reset Extruder
;####### 6mm3/s
M117 210°C // 6mm3/s
G0 X85 Y65 Z15.5 F6000
G4 S20; Stabalize
G0 Z0.3 ; Drop down
G1 X110 E20 F300 ;Prime
G1 E-8 F3600; Retract
G0 X125 F6000 ; Wipe
G0 Z0.5 ; Lift
G1 E8 F3600 ; De-Retract
G1 Z10.5 E200 F7.48 ; Extrude
G1 E-8 F3600 ; Retract
G0 Z15.5; Lift
G0 X85 Y65 F6000
G92 E0 ; Reset Extruder
;####### 8mm3/s
M117 210°C // 8mm3/s
G0 X85 Y95 Z15.5 F6000
G4 S20; Stabalize
G0 Z0.3 ; Drop down
G1 X110 E20 F300 ;Prime
G1 E-8 F3600; Retract
G0 X125 F6000 ; Wipe
G0 Z0.5 ; Lift
G1 E8 F3600 ; De-Retract
G1 Z10.5 E200 F9.98 ; Extrude
G1 E-8 F3600 ; Retract
G0 Z15.5; Lift
G0 X85 Y95 F6000
G92 E0 ; Reset Extruder
;####### 10mm3/s
M117 210°C // 10mm3/s
G0 X85 Y125 Z15.5 F6000
G4 S20; Stabalize
G0 Z0.3 ; Drop down
G1 X110 E20 F300 ;Prime
G1 E-8 F3600; Retract
G0 X125 F6000 ; Wipe
G0 Z0.5 ; Lift
G1 E8 F3600 ; De-Retract
G1 Z10.5 E200 F12.47 ; Extrude
G1 E-8 F3600 ; Retract
G0 Z15.5; Lift
G0 X85 Y125 F6000
G92 E0 ; Reset Extruder
;####### 12mm3/s
M117 210°C // 12mm3/s
G0 X85 Y155 Z15.5 F6000
G4 S20; Stabalize
G0 Z0.3 ; Drop down
G1 X110 E20 F300 ;Prime
G1 E-8 F3600; Retract
G0 X125 F6000 ; Wipe
G0 Z0.5 ; Lift
G1 E8 F3600 ; De-Retract
G1 Z10.5 E200 F14.97 ; Extrude
G1 E-8 F3600 ; Retract
G0 Z15.5; Lift
G0 X85 Y155 F6000
G92 E0 ; Reset Extruder
;####### 14mm3/s
M117 210°C // 14mm3/s
G0 X85 Y185 Z15.5 F6000
G4 S20; Stabalize
G0 Z0.3 ; Drop down
G1 X110 E20 F300 ;Prime
G1 E-8 F3600; Retract
G0 X125 F6000 ; Wipe
G0 Z0.5 ; Lift
G1 E8 F3600 ; De-Retract
G1 Z10.5 E200 F17.46 ; Extrude
G1 E-8 F3600 ; Retract
G0 Z15.5; Lift
G0 X85 Y185 F6000
G92 E0 ; Reset Extruder
;####### 16mm3/s
M117 210°C // 16mm3/s
G0 X85 Y215 Z15.5 F6000
G4 S20; Stabalize
G0 Z0.3 ; Drop down
G1 X110 E20 F300 ;Prime
G1 E-8 F3600; Retract
G0 X125 F6000 ; Wipe
G0 Z0.5 ; Lift
G1 E8 F3600 ; De-Retract
G1 Z10.5 E200 F19.96 ; Extrude
G1 E-8 F3600 ; Retract
G0 Z15.5; Lift
G0 X85 Y215 F6000
G92 E0 ; Reset Extruder
;####### 240C
G4 S0 ; Dwell
M109 S240
;####### 2mm3/s
M117 200°C // 2mm3/s
G0 X165 Y5 Z15.5 F6000
G4 S20; Stabalize
G0 Z0.3 ; Drop down
G1 X190 E20 F300 ;Prime
G1 E-8 F3600; Retract
G0 X205 F6000 ; Wipe
G0 Z0.5 ; Lift
G1 E8 F3600 ; De-Retract
G1 Z10.5 E200 F2.49 ; Extrude
G1 E-8 F3600 ; Retract
G0 Z15.5; Lift
G0 X165 Y5 F6000
G92 E0 ; Reset Extruder
;####### 4mm3/s
M117 200°C // 4mm3/s
G0 X165 Y35 Z15.5 F6000
G4 S20; Stabalize
G0 Z0.3 ; Drop down
G1 X190 E20 F300 ;Prime
G1 E-8 F3600; Retract
G0 X205 F6000 ; Wipe
G0 Z0.5 ; Lift
G1 E8 F3600 ; De-Retract
G1 Z10.5 E200 F4.99 ; Extrude
G1 E-8 F3600 ; Retract
G0 Z15.5; Lift
G0 X165 Y35 F6000
G92 E0 ; Reset Extruder
;####### 6mm3/s
M117 200°C // 6mm3/s
G0 X165 Y65 Z15.5 F6000
G4 S20; Stabalize
G0 Z0.3 ; Drop down
G1 X190 E20 F300 ;Prime
G1 E-8 F3600; Retract
G0 X205 F6000 ; Wipe
G0 Z0.5 ; Lift
G1 E8 F3600 ; De-Retract
G1 Z10.5 E200 F7.48 ; Extrude
G1 E-8 F3600 ; Retract
G0 Z15.5; Lift
G0 X165 Y65 F6000
G92 E0 ; Reset Extruder
;####### 8mm3/s
M117 200°C // 8mm3/s
G0 X165 Y95 Z15.5 F6000
G4 S20; Stabalize
G0 Z0.3 ; Drop down
G1 X190 E20 F300 ;Prime
G1 E-8 F3600; Retract
G0 X205 F6000 ; Wipe
G0 Z0.5 ; Lift
G1 E8 F3600 ; De-Retract
G1 Z10.5 E200 F9.98 ; Extrude
G1 E-8 F3600 ; Retract
G0 Z15.5; Lift
G0 X165 Y95 F6000
G92 E0 ; Reset Extruder
;####### 10mm3/s
M117 200°C // 10mm3/s
G0 X165 Y125 Z15.5 F6000
G4 S20; Stabalize
G0 Z0.3 ; Drop down
G1 X190 E20 F300 ;Prime
G1 E-8 F3600; Retract
G0 X205 F6000 ; Wipe
G0 Z0.5 ; Lift
G1 E8 F3600 ; De-Retract
G1 Z10.5 E200 F12.47 ; Extrude
G1 E-8 F3600 ; Retract
G0 Z15.5; Lift
G0 X165 Y125 F6000
G92 E0 ; Reset Extruder
;####### 12mm3/s
M117 200°C // 12mm3/s
G0 X165 Y155 Z15.5 F6000
G4 S20; Stabalize
G0 Z0.3 ; Drop down
G1 X190 E20 F300 ;Prime
G1 E-8 F3600; Retract
G0 X205 F6000 ; Wipe
G0 Z0.5 ; Lift
G1 E8 F3600 ; De-Retract
G1 Z10.5 E200 F14.97 ; Extrude
G1 E-8 F3600 ; Retract
G0 Z15.5; Lift
G0 X165 Y155 F6000
G92 E0 ; Reset Extruder
;####### 14mm3/s
M117 200°C // 14mm3/s
G0 X165 Y185 Z15.5 F6000
G4 S20; Stabalize
G0 Z0.3 ; Drop down
G1 X190 E20 F300 ;Prime
G1 E-8 F3600; Retract
G0 X205 F6000 ; Wipe
G0 Z0.5 ; Lift
G1 E8 F3600 ; De-Retract
G1 Z10.5 E200 F17.46 ; Extrude
G1 E-8 F3600 ; Retract
G0 Z15.5; Lift
G0 X165 Y185 F6000
G92 E0 ; Reset Extruder
;####### 16mm3/s
M117 200°C // 16mm3/s
G0 X165 Y215 Z15.5 F6000
G4 S20; Stabalize
G0 Z0.3 ; Drop down
G1 X190 E20 F300 ;Prime
G1 E-8 F3600; Retract
G0 X205 F6000 ; Wipe
G0 Z0.5 ; Lift
G1 E8 F3600 ; De-Retract
G1 Z10.5 E200 F19.96 ; Extrude
G1 E-8 F3600 ; Retract
G0 Z15.5; Lift
G0 X165 Y215 F6000
G92 E0 ; Reset Extruder
;####### End G-Code
G0 X245 Y245 ; Move to Corner
M104 S0 T0 ; Turn Off Hotend
M140 S0 ; Turn Off Bed
M84

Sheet: SampleEvaluation
 |  | Test 1
 | Printer | Ender-7 Pro
 | Material | Filament PLA
 | Temperature / °C | 220 | 210 | 200
 | Flow rate / mm³/s | weights / g
Input | 2 | 0.587 | 0.562 | 0.580
 | 4 | 0.578 | 0.569 | 0.574
 | 6 | 0.578 | 0.566 | 0.566
 | 8 | 0.580 | 0.568 | 0.553
 | 10 | 0.569 | 0.566 | 0.557
 | 12 | 0.580 | 0.557 | 0.541
 | 14 | 0.564 | 0.554 | 0.533
 | 16 | 0.546 | 0.542 | 0.516
Underextrusion Amount | 2 | 0% | 0% | 0%
 | 4 | -1.533219761% | 1.245551601% | -1.034482759%
 | 6 | -1.533219761% | 0.7117437722% | -2.413793103%
 | 8 | -1.192504259% | 1.067615658% | -4.655172414%
 | 10 | -3.066439523% | 0.7117437722% | -3.965517241%
 | 12 | -1.192504259% | -0.8896797153% | -6.724137931%
 | 14 | -3.918228279% | -1.423487544% | -8.103448276%
 | 16 | -6.984667802% | -3.558718861% | -11.03448276%
Real Flow | 2 | 2.0 | 2.0 | 2.0
 | 4 | 3.9 | 4.0 | 4.0
 | 6 | 5.9 | 6.0 | 5.9
 | 8 | 7.9 | 8.1 | 7.6
 | 10 | 9.7 | 10.1 | 9.6
 | 12 | 11.9 | 11.9 | 11.2
 | 14 | 13.5 | 13.8 | 12.9
 | 16 | 14.9 | 15.4 | 14.2
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

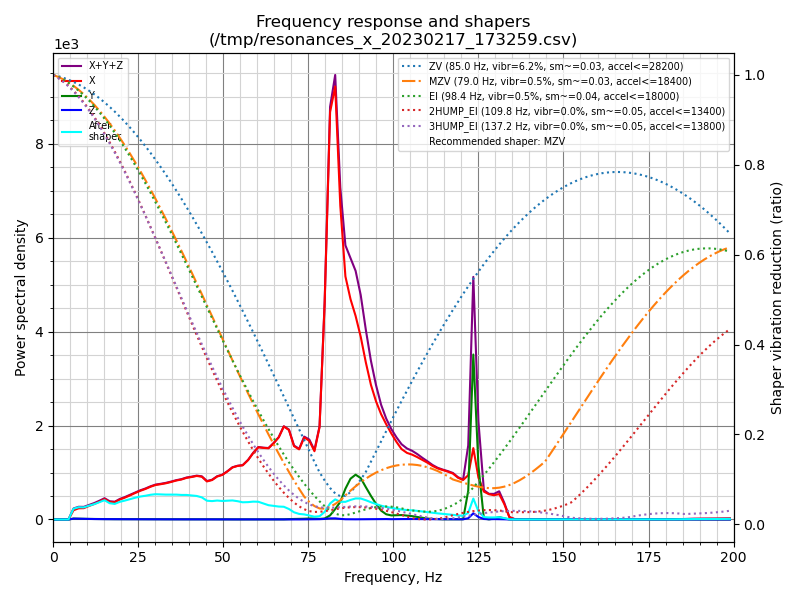
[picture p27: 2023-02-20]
images/shaper_calibrate_x.png

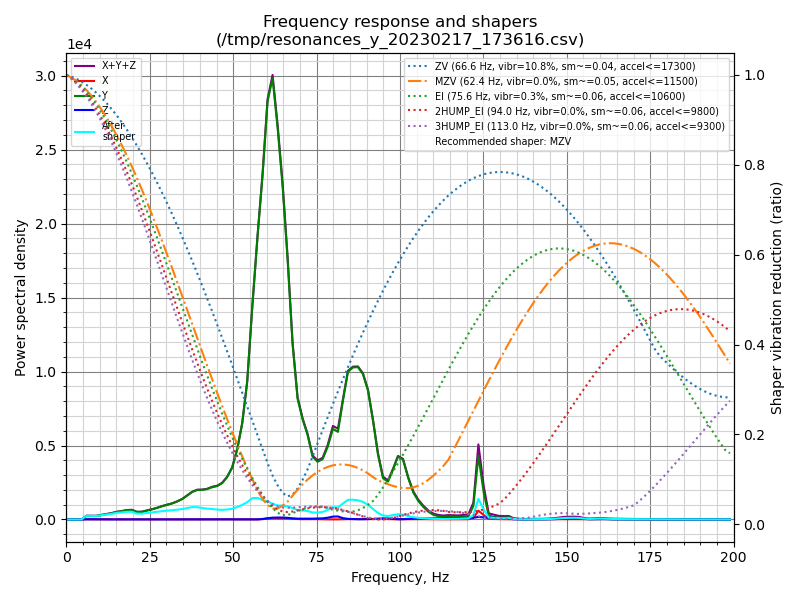
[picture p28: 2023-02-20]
images/shaper_calibrate_y.png

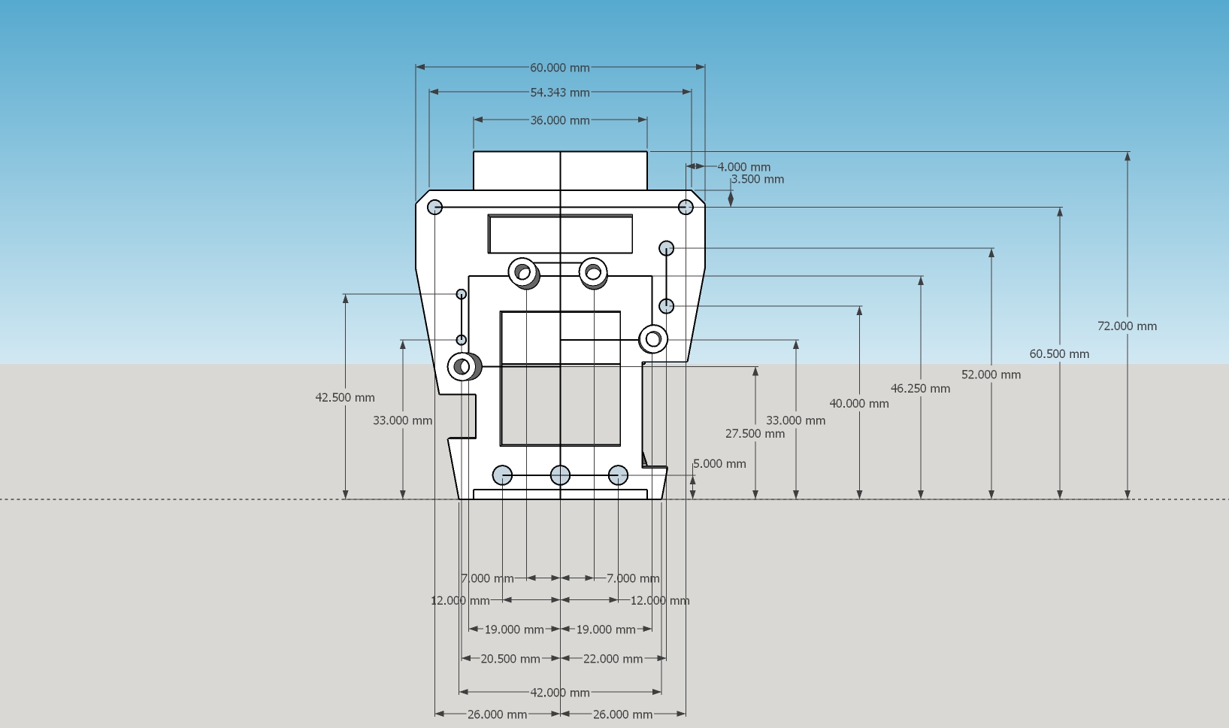
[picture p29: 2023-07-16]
20230716_hotendupgrade/20230710_ender-7_carrage_measurements.jpg

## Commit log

2023-02-18 Create 03_Testing & Calibration.txt
2023-02-18 Update 03_Testing & Calibration.txt
2023-02-19 Create 05_Extruder maximum flow
2023-02-19 Update 05_Extruder maximum flow
2023-02-21 Update 05_Extruder maximum flow.txt
2023-05-08 Update 02_Klipper config and install.txt
    [02_Klipper config and install.txt]
